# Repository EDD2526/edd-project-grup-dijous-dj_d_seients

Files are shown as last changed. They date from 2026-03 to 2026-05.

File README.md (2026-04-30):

View this project on [CADLAB.io](https://cadlab.io/project/30198). 

# Projecte Grup D (Dijous-tarda): Seients

>**Autors:
- Joan Martínez [@JoaanMG]
- Manel Frías [@manelfriass]
- Joan Heras [@jheraas]

>**Versió: V5.0 (final)

----------

## Objectiu

En primer lloc cal explicar que estem davant de l'elaboració d’un mòdul crític per a la seguretat i el funcionament del vehicle. El sistema de SEIENTS DIGITALS és la interfície entre l'energia del cotxe i la seguretat del conductor.
Per tant ens basarem en aquests puts adjuntats al guió:

  a) 3 motors (posició, alçada, reclinació) amb els seus finals de carrera.
  b) Calefacció del seient. 
  c) Sensor digital de cinturons.
  d) Memòria externa no volàtil per guardar posicions pre-programades.

>PCB per ...

L'objectiu principal és dissenyar i fabricar una PCB funcional per a la gestió del subsistema de seients elèctrics d'un vehicle, complint els següents punts:

- Controlar 3 motors del seient:
- Posició longitudinal, alçada, Inclinació del respatller
- Detectar finals de carrera per evitar sobrecàrregues mecàniques.
- Implementar calefacció del seient amb control electrònic.
- Detectar estat del cinturó de seguretat.
- Guardar i recuperar posicions programades del seient mitjançant memòria no volàtil.
- Permetre la interacció de l’usuari amb botonera.
- Comunicar-se amb la xarxa del vehicle via bus CAN.
- Permetre monitorització i debug via USART.

## Diagrama de blocs

### Descripció/funcionalitat de cada bloc

  - ALIMENTACIÓ: El sistema s’alimenta a partir de la bateria del vehicle (12V). Aquesta tensió es condiciona mitjançant dues etapes. Això permet alimentar:

    * Microcontrolador.
    * Sensors.
    * Comunicacions.
 
  - UART: per debug i monitorització.

  - MICROCONTROLADOR: És el nucli del sistema, encarregat de: Processar les entrades (botons i sensors), controlar els motors, gestionar la comunicació amb altres mòduls. També gestiona diferents interfícies:

    * GPIO → botonera i sensors.
    * PWM → control de motors i calefacció.
    * I2C → memòria i sensor de temperatura.
    * CAN → comunicació amb el vehicle.
    * UART → debug.

  - BOTONERA: Permet a l’usuari controlar el seient:

    * Posició.
    * Alçada.
    * Reclinació.
    
  - SENSORS: de temperatura i cinturons.

  - SISTEMA DE MOTORS.

  - SISTEMA DE CALEFACCIÓ.

  - MEMÒRIA.

  - COMUNICACIÓNS.

-----------

## Requisits / Especificacions

  * Alimentació; 12V, regulada 5V
  * Microcontrolador PIC18xxxxxxxxx
  * ...

-----------

## Components

| Descripci&#243; | Ref | Package |Datasheet | Prove&#239;dor | Value | Preu | Unitats |

| Capacitor | KAF21BR71H104JM | SMD | [Enllaç](https://www.mouser.com/datasheet/3/5926/1/AutoMLCCKAF.pdf) | 100 nF| 0,078 € | x21 |

| Capacitor | KAF21BR71H104JM | SMD | [Enllaç](https://www.mouser.com/datasheet/3/5926/1/AutoMLCCKAF.pdf) | 220 uF| 0,078 € | x2 |

| Capacitor | KAF21BR71H104JM | SMD | [Enllaç](https://www.mouser.com/datasheet/3/5926/1/AutoMLCCKAF.pdf) | 10 uF| 0,078 € | x2 |

| Capacitor | KAF21BR71H104JM | THT | [Enllaç](https://www.mouser.com/datasheet/3/5926/1/AutoMLCCKAF.pdf) | 100 nF| 0,078 € | x2 |

| Capacitor | KAF21BR71H104JM | THT | [Enllaç](https://www.mouser.com/datasheet/3/5926/1/AutoMLCCKAF.pdf) | 100 nF| 0,078 € | x2 |

| Capacitor | KAF21BR71H104JM | SMD | [Enllaç](https://www.mouser.com/datasheet/3/5926/1/AutoMLCCKAF.pdf) | 0.1 uF| 0,078 € | x3 |

| --- | --- | --- | --- | ---| --- | --- |

| Exemple | XYZ1234 | SOT-23 | [Enllaç](https://...) | DigiKey | 2 |

 | Microcontrolador | PIC18F26Q83-I/SS | SOIC-28 |[Datasheet](https://www.mouser.es/datasheet/2/268/PIC18F27_47_57Q83_Preliminary_Data_Sheet_40002265B-2887591.pdf) | [Mouser](https://www.mouser.es/c/?q=PIC18F27Q83-I%2FSO)| 2,17&euro;| 1x |
| XTAL-Ressonador | CSTCR7M99G53-R0 | SMD |[Datasheet](https://www.mouser.es/datasheet/2/281/p16e-522700.pdf) | [Mouser](https://www.mouser.es/ProductDetail/Murata-Electronics/CSTCR7M99G53-R0?qs=Zd9RUO93%2Fo7cnwzsujIkpA%3D%3D)  | 0,27&euro; | 1x |

-----------

## Software

### Eines:

  * KiCad 9.0 o superior
  * 

### Configuraci&#243; :

  * 

### Funcionalitats:

  - Controlar 3 motors del seient:
  - Posició longitudinal, alçada, Inclinació del respatller
  - Detectar finals de carrera per evitar sobrecàrregues mecàniques.
  - Implementar calefacció del seient amb control electrònic.
  - Detectar estat del cinturó de seguretat.
  - Guardar i recuperar posicions programades del seient mitjançant memòria no volàtil.
  - Permetre la interacció de l’usuari amb botonera.
  - Comunicar-se amb la xarxa del vehicle via bus CAN.
  - Permetre monitorització i debug via USART

-----------

## Historial de canvis:

23/03/2026 a les 14:07
Al dia d'avui s'ha modificat el diagrama de blocs: hem ajustat petites coses per finalitzar el diagrama de blocs definitiu.

23/03/2026 a les 17:22
Tan bon punt hem modificat el digrama de blocs, al dia d'avui també s'ha modificat la part sensors: hem incorporat l'esquemàtic preliminar una vegada ajustat el diagrama de blocs. Incorporats el TMP102 (sensor de temperatura) i el Hall A3144 (sensor digital dels cinturons).

24/03/2026 a les 14:07
Al dia d'avui s'ha modificat la part d'alimentació: hem incorporat dues coses importants: FUSIBLE i DIODES TVS. Hem modificat els possibles errors mitjançant una escombrada de l'ERC. Alimentació (ACABAT AL 100%).

24/03/2026 a les 18:48
S'ha modificat la part de SENSORS: una vegada incorporats el TMP102 (sensor de temperatura) i el Hall A3144 (sensor digital dels cinturons) hem realitzat la incorporación dels components: resistències pull-up, capacitats de desacoblament, ...

25/03/2026 a les 09:35
Al dia d'avui s'ha modificat la part de sensors: hem incorporat etiquetes i hem modificat algunes connexions degut a problemes amb l'ERC, SENSORS (ACABAT AL 100%).

25/03/2026 a les 1O:07
S'ha modificat la part de SENSORS: hem finalitzat tot l'esquemàtic d'aquesta part i donem per acabada la part de SENSORS.

25/03/2026 a les 09:35
Efectuada la simulació per demostrar el funcionamenten del LM1117-3.3 (part d'ALIMENTACIÓ) a LTSpice.

| Data | Autor | Branch | Versi&#243; | Descripci&#243; |
| --- | --- | --- | --- | --- |
|  28/03/2023 | mlopez | Master | initial commit | Primera versi&#243; d'esquem&#224;tic i selecci&#243; de components |
E s t a   e s   u n a   l   n e a   d e   p r u e b a   p a r a   e l   r e p o s i t o r i o

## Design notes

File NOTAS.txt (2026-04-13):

SECCIONES:

ALIMENTACIO
POTENCIA (DRIVERS, MOSFET)
SENSORS
DIGITAL/MICROCONTROLADOR/BOTONERA

CALEFACCION METER RELÉ

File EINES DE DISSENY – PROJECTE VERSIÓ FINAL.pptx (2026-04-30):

## EINES DE DISSENY PROJECTE: GRUP D TARDA (SEIENTS)

Joan Martínez
Joan Heras
Manel Frías

## 01 CONTINGUTS 04 03 02

OBJECTIUS DEL PROJECTE

DIAGRAMA DE BLOCS

ESQUEMÀTIC I COMPONENTS

SIMULACIONS

## 05 07 06

LAYOUT I PCB

BOM I PRESSUPOST

RESOURCES

## 01 OBJECTIUS DEL PROJECTE

## OBJECTIUS DEL PROJECTE (Característiques):

En primer lloc cal explicar que estem davant de l'elaboració d’un mòdul crític per a la seguretat i el funcionament del vehicle. El sistema de SEIENTS DIGITALS és la interfície entre l'energia del cotxe i la seguretat del conductor. Per tant ens basarem en aquests puts adjuntats al guió:
a) 3 motors (posició, alçada, reclinació) amb els seus finals de carrera.
b) Calefacció del seient.
c) Sensor digital de cinturons.
d) Memòria externa no volàtil per guardar posicions pre-programades.

## OBJECTIUS PRINCIPALS DEL PROJECTE

L'objectiu principal és dissenyar i fabricar una PCB funcional per a la gestió del subsistema de seients elèctrics d'un vehicle, complint els següents punts:
- Controlar 3 motors del seient:
- Posició longitudinal, alçada, Inclinació del respatller
- Detectar finals de carrera per evitar sobrecàrregues mecàniques.
- Implementar calefacció del seient amb control electrònic.
- Detectar estat del cinturó de seguretat.
- Guardar i recuperar posicions programades del seient mitjançant memòria no volàtil.
- Permetre la interacció de l’usuari amb botonera.
- Comunicar-se amb la xarxa del vehicle via bus CAN.
- Permetre monitorització i debug via USART.c

## 02 DIAGRAMA DE BLOCS

## V.2

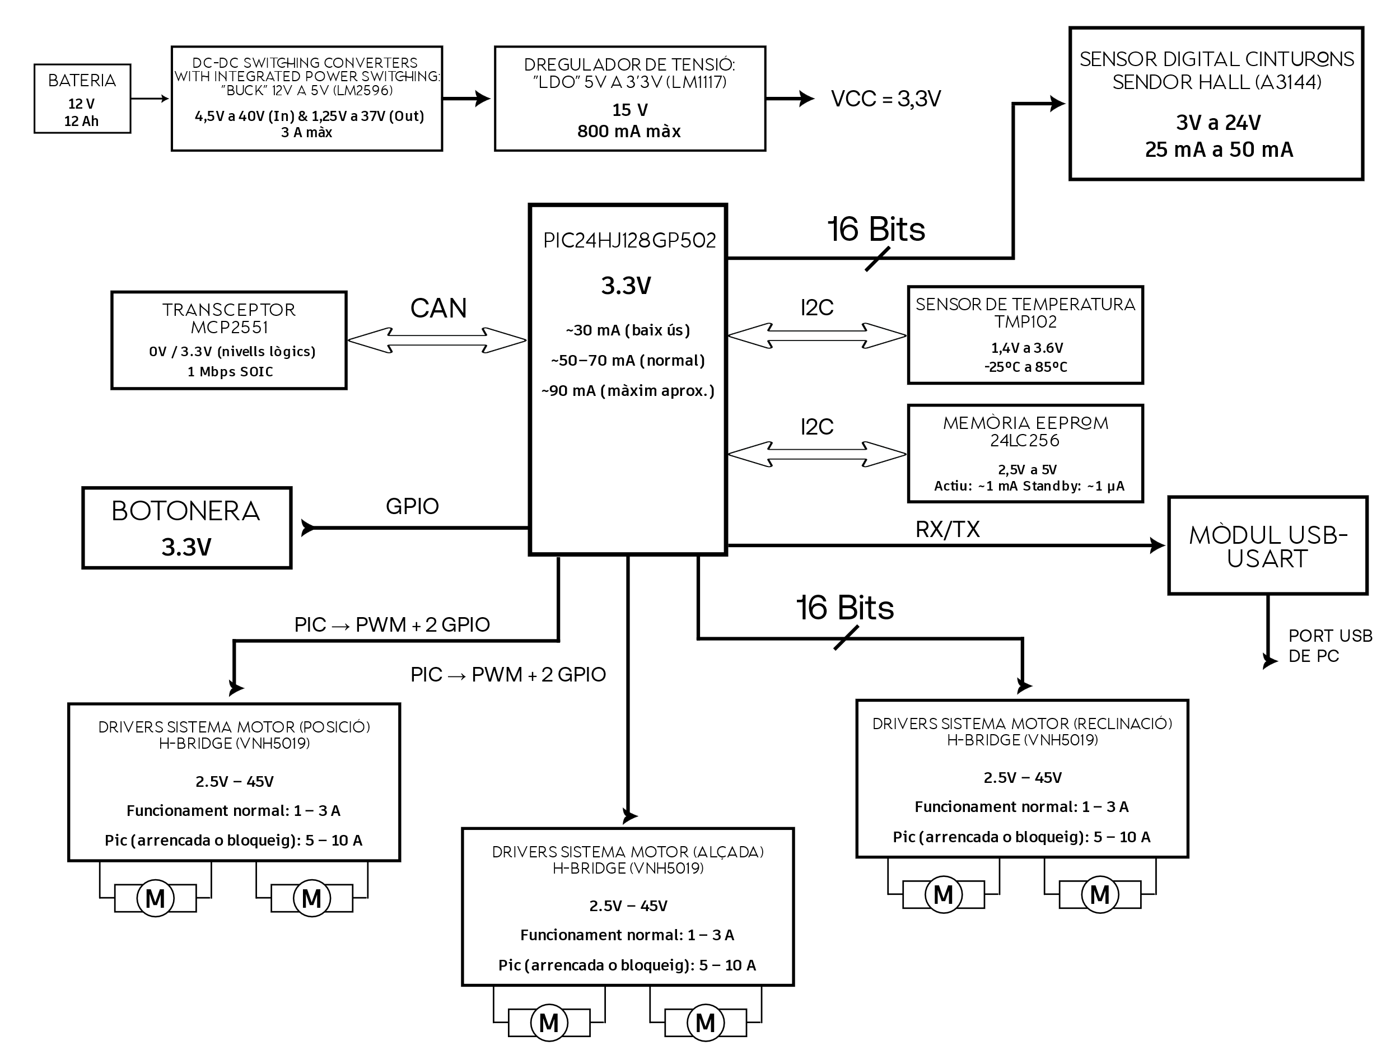
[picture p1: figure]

## V.3

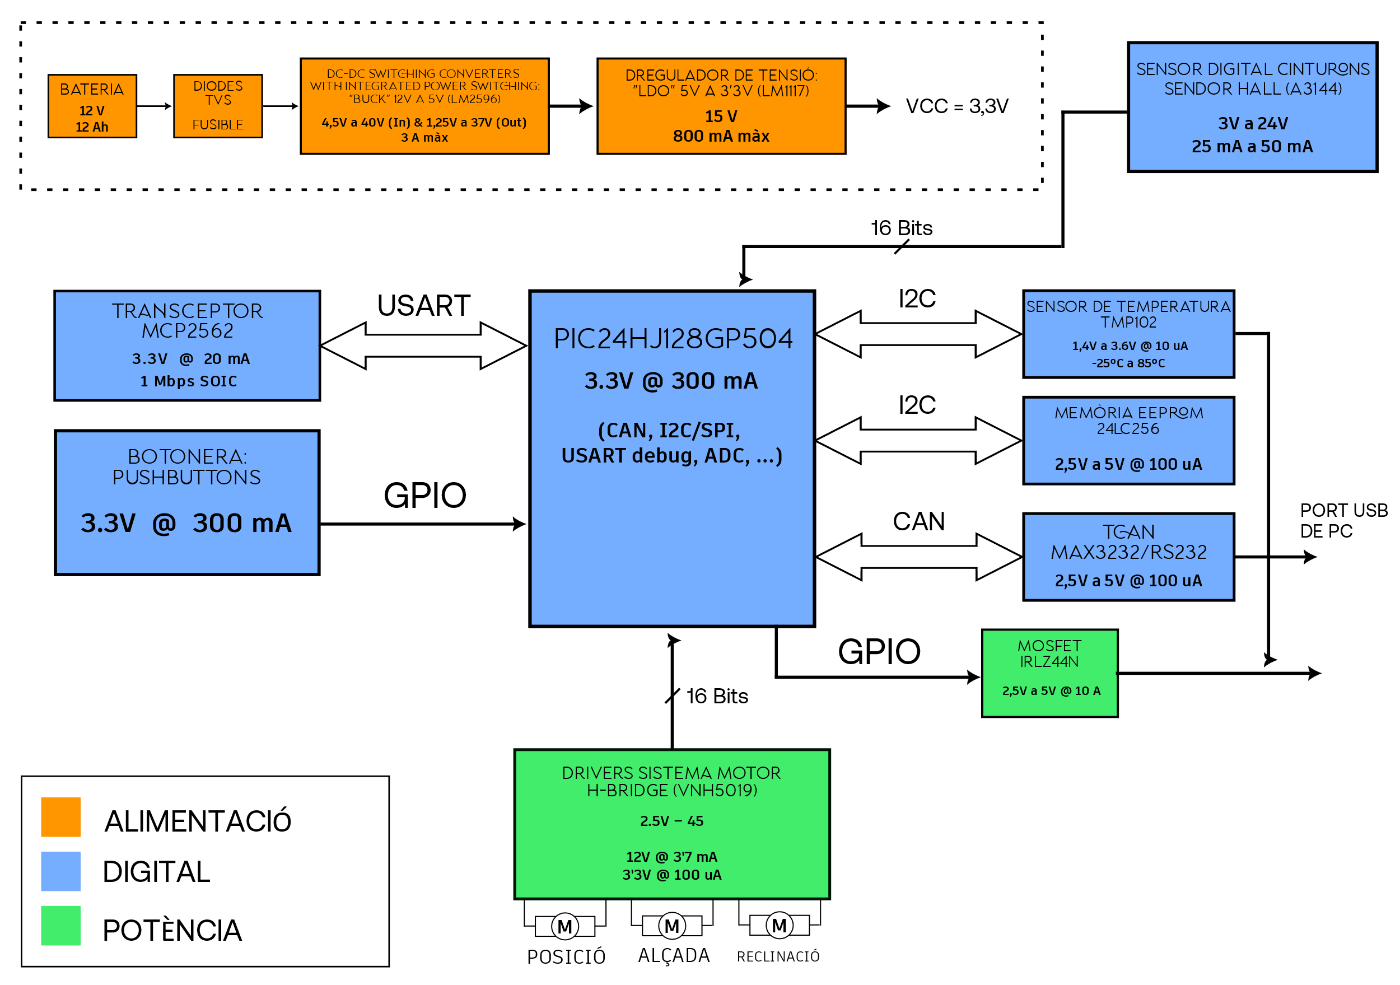
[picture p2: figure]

## ESQUEMÀTIC DEL PROJECTE 03

## ALIMENTACIÓ:

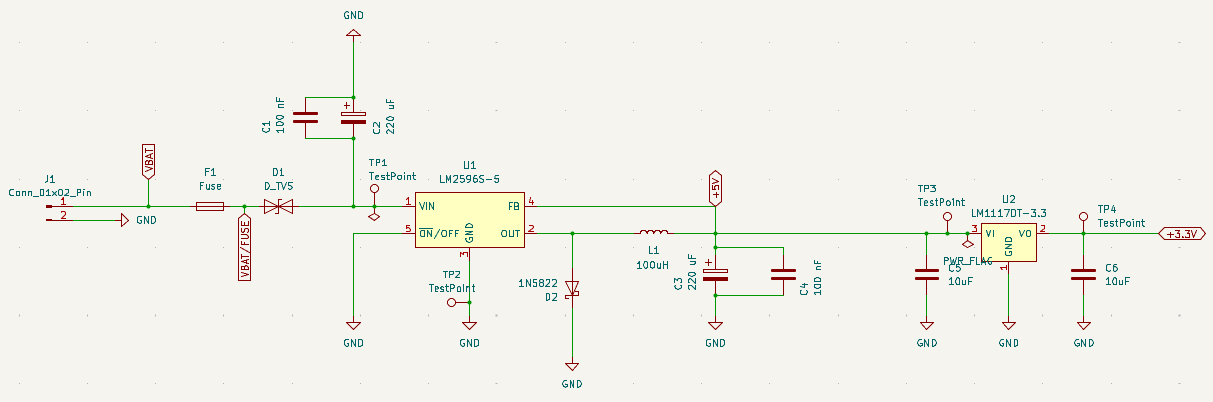
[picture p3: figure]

## SENSORS:

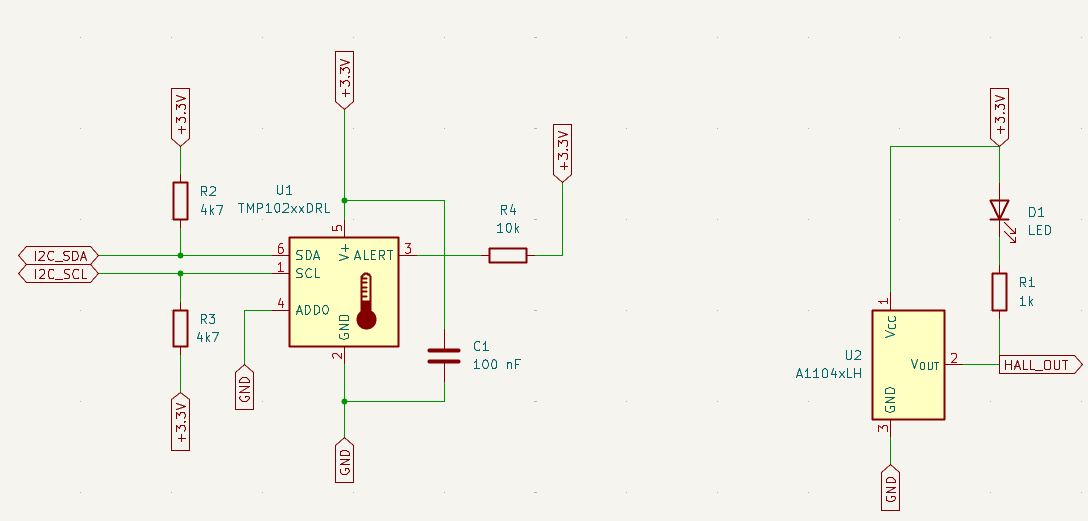
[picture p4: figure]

V.2

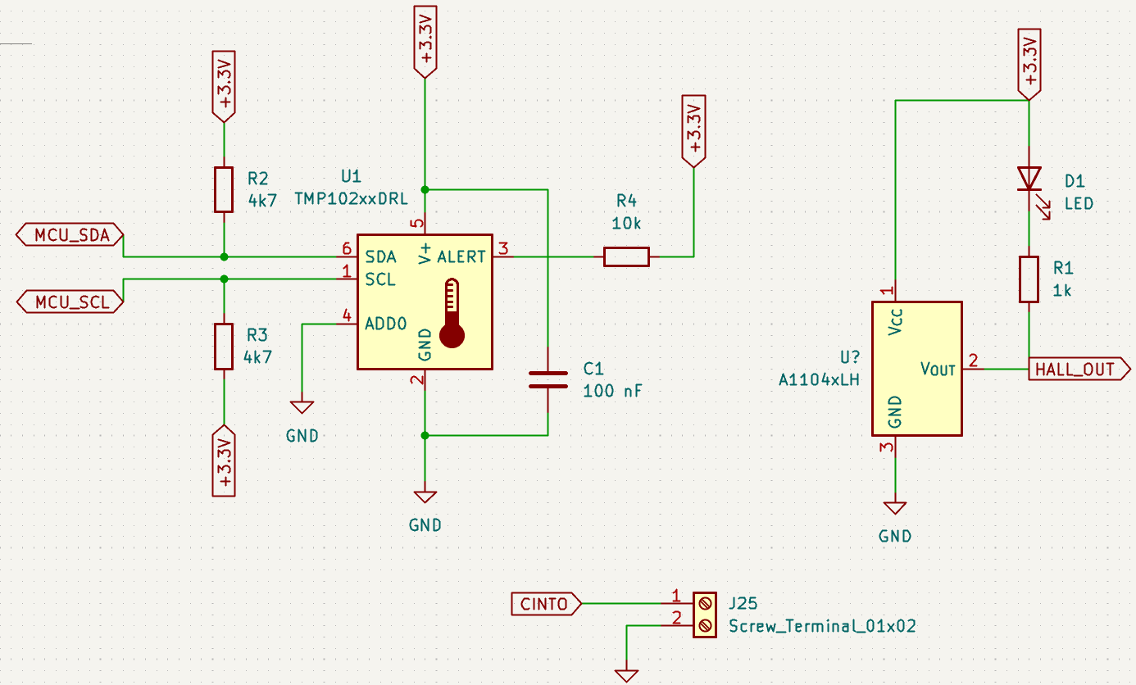
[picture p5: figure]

V.3

## DRIVERS:

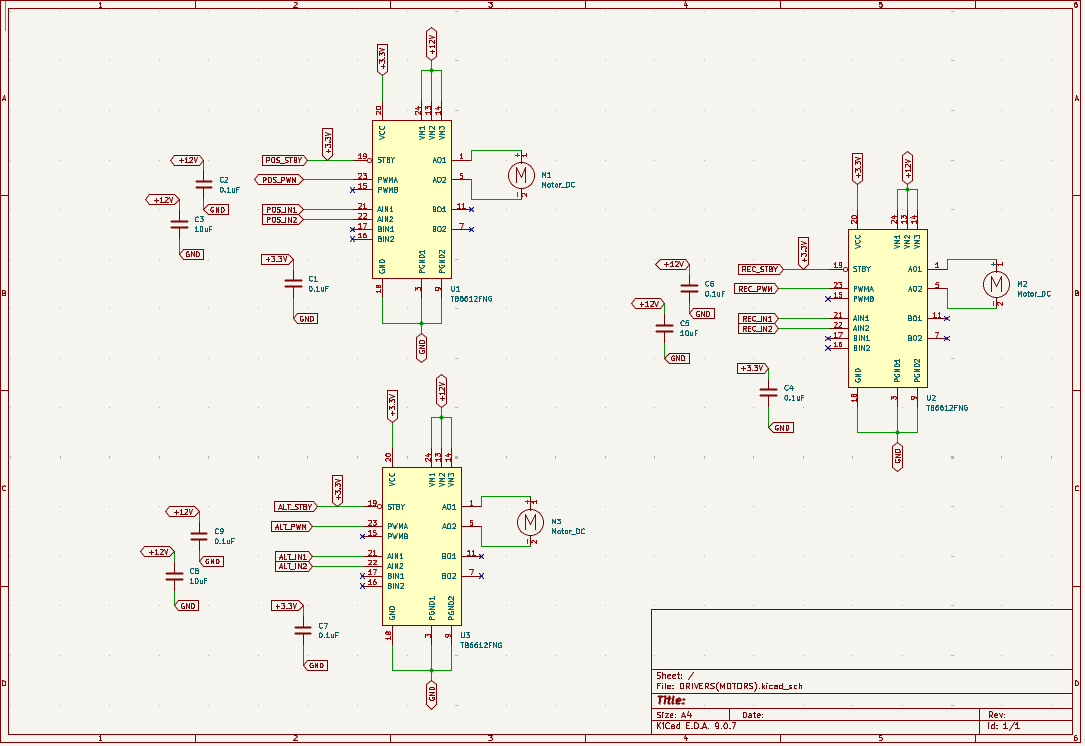
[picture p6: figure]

V.2

## DRIVERS:

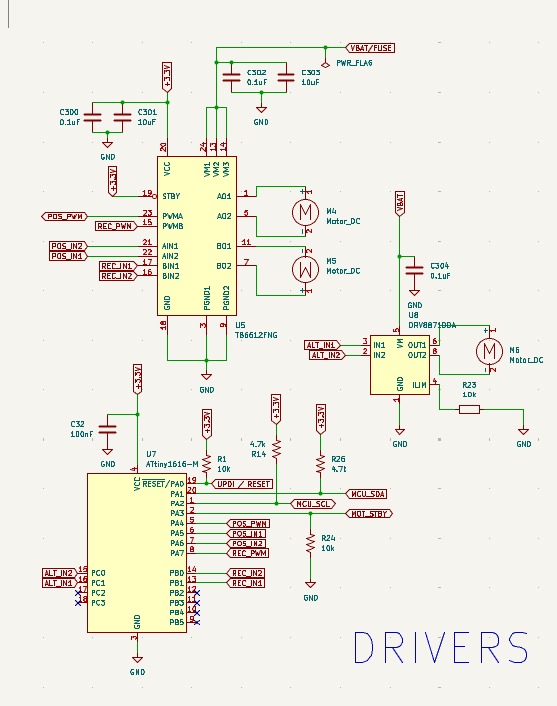
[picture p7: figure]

V.3

## EEPROM:

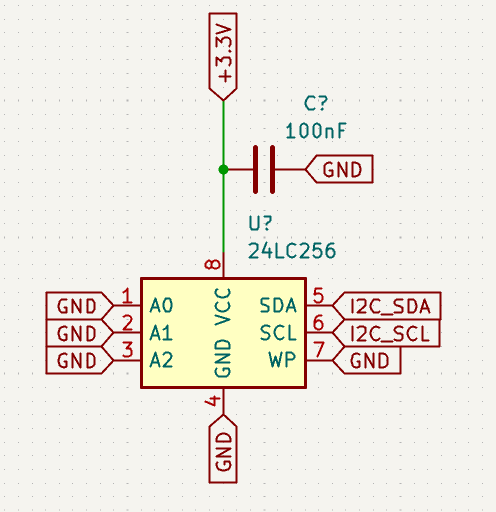
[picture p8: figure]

V.2

## EEPROM:

V.3

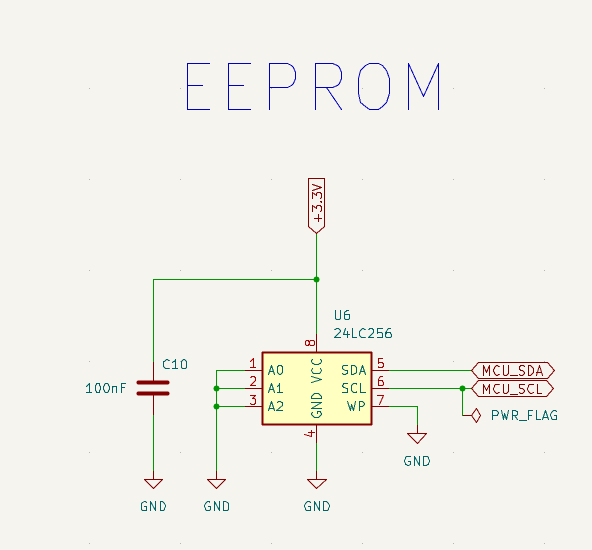
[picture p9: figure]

## MOSFET:

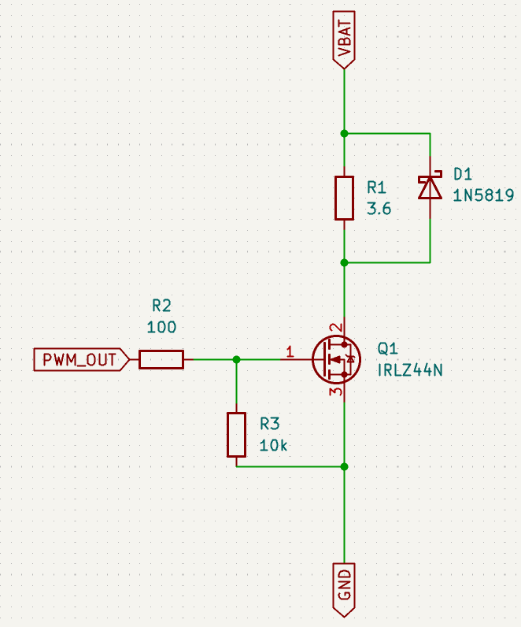
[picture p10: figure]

V.2

## MOSFET:

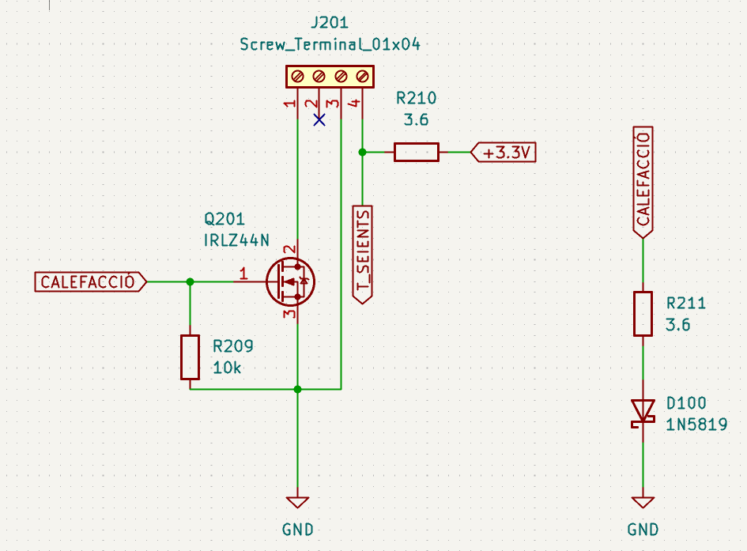
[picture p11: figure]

V.3

## CAN/DE-9:

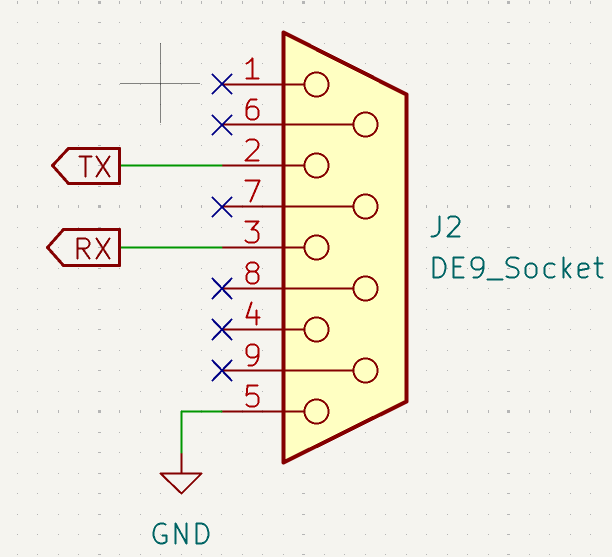
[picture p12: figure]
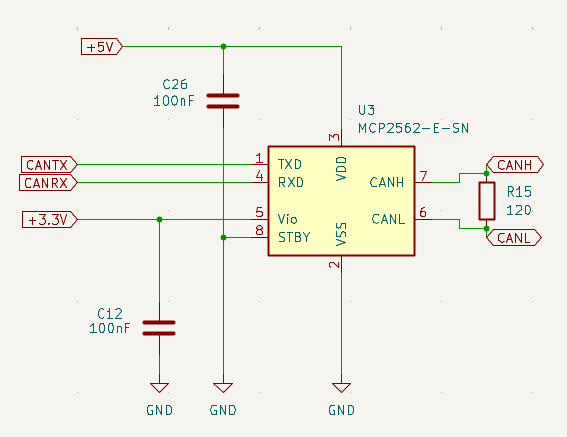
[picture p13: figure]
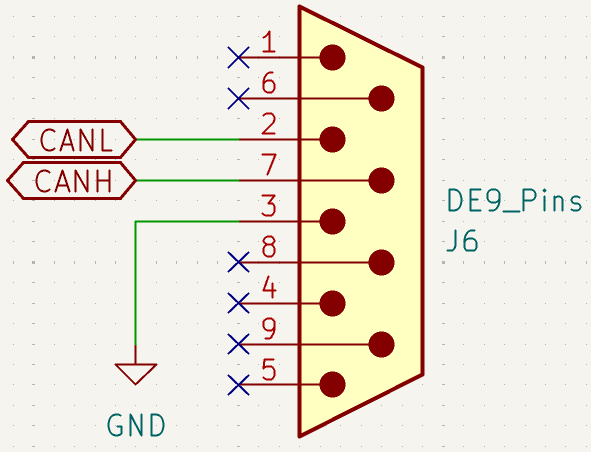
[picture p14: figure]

## BOTONERA:

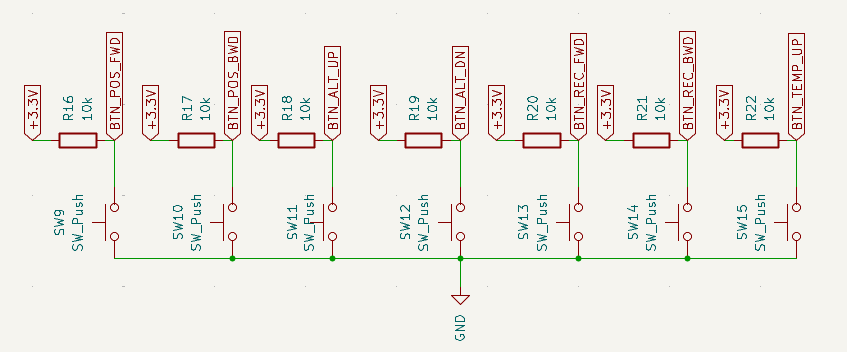
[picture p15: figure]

## MICROCONTROLADOR:

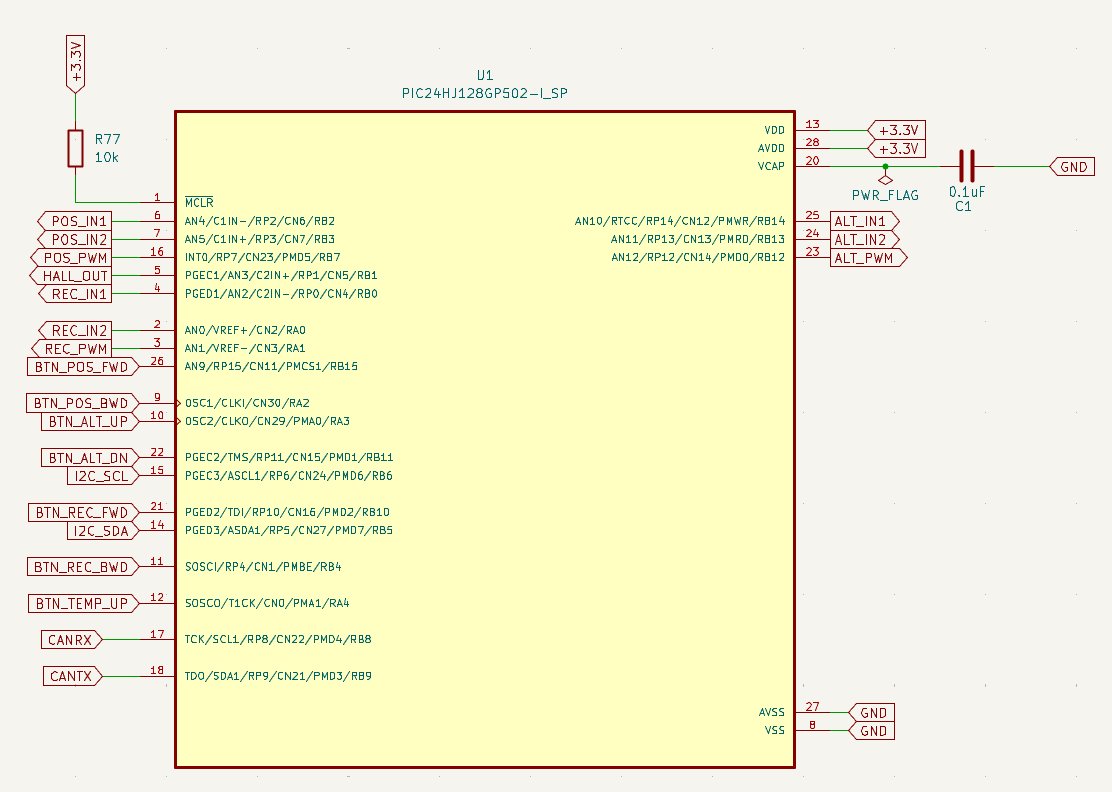
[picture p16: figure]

V.2

## MICROCONTROLADOR:

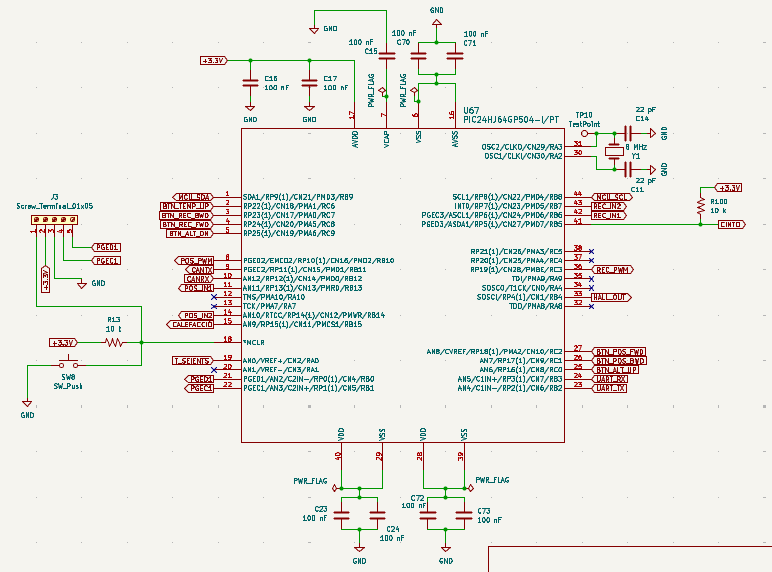
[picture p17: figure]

V.3

## SIMULACIONS LTSPICE 04

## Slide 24

En particular, s’ha simulat el regulador de tensió (LM1117) amb diferents condicions de càrrega per comprovar la seva capacitat de mantenir una tensió estable de 3.3V davant variacions de corrent:

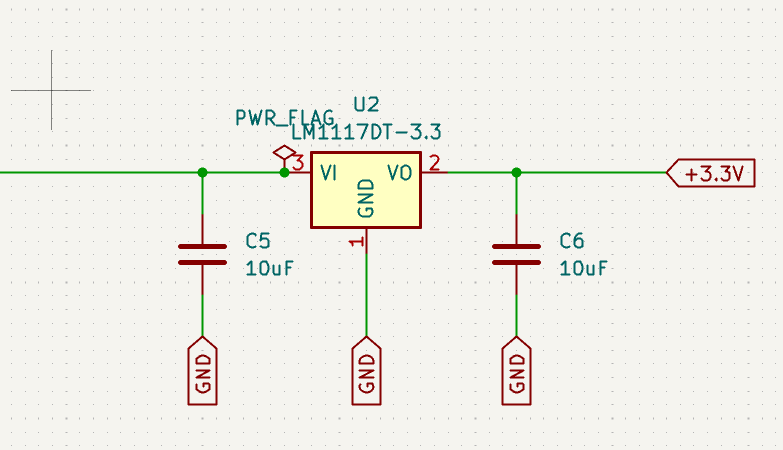
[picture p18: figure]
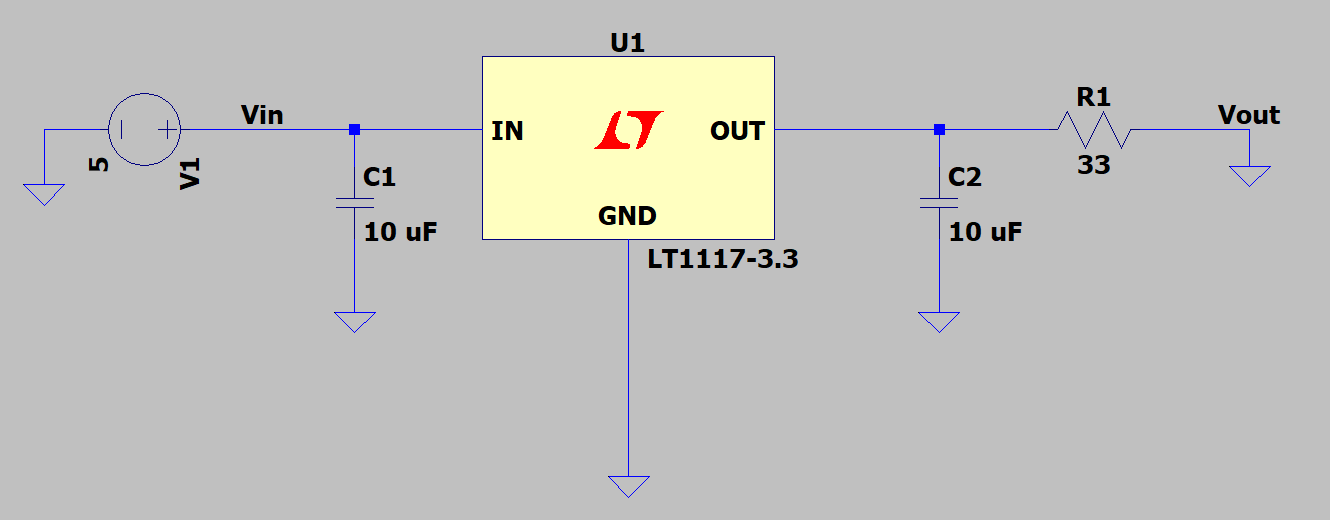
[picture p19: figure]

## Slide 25

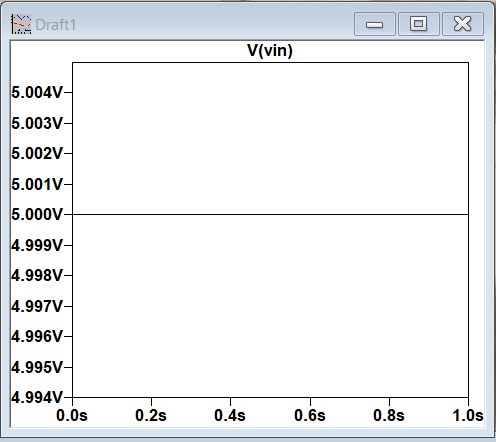
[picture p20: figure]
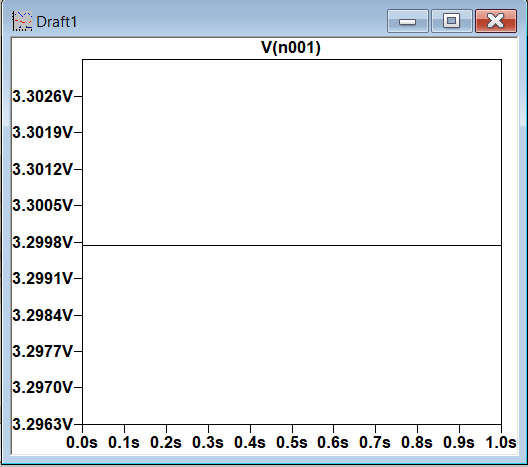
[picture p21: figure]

## LAYOUT I PCB 05

## BOM I COSTOS 06

## PRESSUPOST DE FABRICACIÓ

Vam procedir a crear un compte a Mouser Electronics, Inc. Vam crear un projecte nou el qual es va exportar el BOM creat pel KICad i tots els components que hem utilitzat van quedar enregistrats en un altre arxiu de fulla de càlcul (.xlxs).

## PRESSUPOST DE FABRICACIÓ:

Com a idea general, el cost del projecte no és fix, sinó que depèn principalment de:

VOLUM DE PRODUCCIÓ

## PRESSUPOST DE FABRICACIÓ:

l el projecte demana analitzar:
    - x10 unitats
    - x50 unitats
    - x1.000 unitats
    - x20.000 unitats

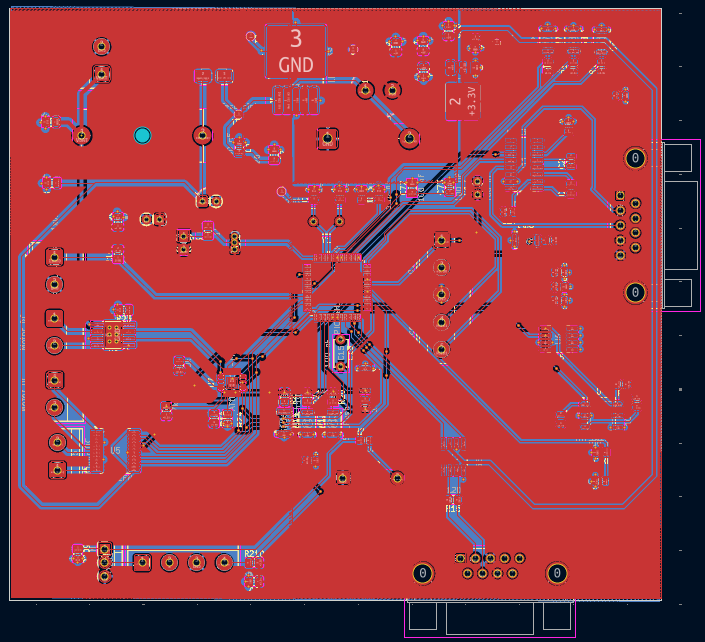
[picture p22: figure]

## PRESSUPOST DE FABRICACIÓ:

Volum (per unitats) | Cost total
x1 unitats | 63,863 €
x10 unitats | 638,63 €
x50 unitats | 3193.15 €
x1.000 unitats | 63.863 €
x20.000 unitats | 1.277.260 €

## PRESSUPOST DE FABRICACIÓ:

1. Components (BOM)
2. Fabricació de la PCB
3. Muntatge

Segons el document, el cost es divideix en:

## PRESSUPOST DE FABRICACIÓ:

l què passa amb el cost?
- A mesura que augmenta la producció:
- L’anàlisi de costos mostra que el preu del sistema depèn fortament del volum de producció, reduint-se significativament en producció massiva gràcies a economies d’escala i processos de fabricació automatitzats.

EL COST PER UNITAT BAIXA

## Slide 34

COMPONENTS | PREU (€)
MAX3232 | 9.15
Regulador switching | 5.99
Microcontrolador | 5.74
Inductor | 4.68
Connector D-Sub | 2.91
Terminal blocks | 2.39
Driver motor | 2.35
MOSFET | 1.52

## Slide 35

El cost total creix linealment amb el volum, però el cost per unitat disminuiria en producció real gràcies a economies d’escala.

## QUINA CONCLUSIÓ PODEM EXTREURE ?

En primer lloc podem afirmar que els components passius dominen la taula. El cost per PCB és d’aproximadament 54€, dominat pels components actius del sistema. Els components més cars són el microcontrolador, els drivers i els reguladors, mentre que els passius tenen un impacte econòmic molt reduït
Finalment, si s’efectua una producció massiva, el cost per unitat es reduiria significativament gràcies a descomptes i optimització del procés de fabricació.

## RESOURCES 07

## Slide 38

Webgrafia:
- Microchip Technology. (2012). PIC24HJ128GP502 Family Data Sheet. High-Performance, 16-bit Digital Signal Controllers. [En línia]. Disponible a: microchip.com
- Microchip Technology. (2016). MCP2561/2 High-Speed CAN Transceiver Data Sheet. [En línia].Texas Instruments. (2020). LM1117 800-mA, Low-Dropout Voltage Regulator. [En línia]. Disponible a: ti.com
- Infineon Technologies. (2023). Automotive MOSFETs Selection Guide.
- Vector Informatik GmbH. (2024). CAN Knowledge Base. [web]. vector.com.
- All About Circuits. (2024). Understanding the I2C Bus. [Article tècnic]. Disponible a: allaboutcircuits.com.
- Microchip Developer Help. Getting Started with MPLAB X IDE and XC16 Compiler. [Portal de suport].

## GRÀCIES!

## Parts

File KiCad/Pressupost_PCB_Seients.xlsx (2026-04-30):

Cost total del projecte: Components + PCB + muntatge | Cost total del projecte: Components + PCB + muntatge | Cost total del projecte: Components + PCB + muntatge | Cost total del projecte: Components + PCB + muntatge | Cost total del projecte: Components + PCB + muntatge | Cost total del projecte: Components + PCB + muntatge | Cost total del projecte: Components + PCB + muntatge | Cost total del projecte: Components + PCB + muntatge | Cost total del projecte: Components + PCB + muntatge
Paràmetre | Valor | Notes |  |  |  |  |  |  | Component crític | Cost aproximat | Motiu
Cost BOM per PCB | €65.9150 | Calculat del BOM Mouser: sum(Unit Price × Order Quantity) |  |  |  |  |  |  | RS-232 / UART interface | €9.15 | Component més car del BOM
Juntes SMT per PCB | €220.0000 | Estimació per al càlcul de muntatge |  |  |  |  |  |  | Regulador switching | €5.99 | Etapa d'alimentació
Juntes manuals per PCB | €30.0000 | Connectors/through-hole o muntatge manual |  |  |  |  |  |  | Microcontrolador PIC24 | €5.74 | Control principal
Setup muntatge | €25.0000 | Cost fix |  |  |  |  |  |  | Inductor | €4.68 | Etapa buck
Stencil | €7.8600 | Cost fix |  |  |  |  |  |  | Connector D-Sub | €2.91 | Comunicacions externes
Panel fee | €7.8100 | Cost fix
Cost SMT per junta | €0.0016 | Cost variable
Cost manual per junta | €0.0157 | Cost variable
PCB bare board total | Estimació | Substituir pel pressupost real de JLCPCB quan tingueu Gerbers
Volum | BOM €/PCB | BOM total € | PCB €/PCB | PCB total € | Muntatge €/PCB | Muntatge total € | Cost total €/PCB | Cost total €
10 | €65.92 | €659.15 | €2.50 | €25.00 | €4.89 | €48.90 | €73.31 | €733.05
50 | €65.92 | €3295.75 | €1.40 | €70.00 | €1.64 | €81.82 | €68.95 | €3447.57
1000 | €65.92 | €65915.00 | €0.50 | €500.00 | €0.86 | €863.67 | €67.28 | €67278.67
20000 | €65.92 | €1318300.00 | €0.30 | €6000.00 | €0.83 | €16500.67 | €67.04 | €1340800.67

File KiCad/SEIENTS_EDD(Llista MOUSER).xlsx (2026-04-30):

Mouser Part Number (Input) | Mfr Part Number | Mouser Part Number | Manufacturer Name | Description | Unit Price 1 (EUR) | Price 2 (EUR) | Price 3 (EUR) | Order Quantity | Order Unit Price (EUR) | Price by Order Unit (EUR) | Price 5 (EUR) | Min./Mult. | Availability | Lead Time in Days | Lead Time in Weeks | Lifecycle | NCNR | RoHS | Pb Free | Package Type | Package Quantity | Datasheet URL | Product Image | Design Risk
KAF21BR71H104JM | KAF21BR71H104JM | 581-KAF21BR71H104JM | KYOCERA AVX | Multilayer Ceramic Capacitors MLCC - SMD/SMT Multilayer Ceramic Capacitors MLCC - SMD/SMT Automotive 0805, 100nF, 5%, X7R, 50V | 0,078 € |  |  | 21 | 0,078 € | 1.638 |  | 1/1 | 40.051 | 84 | 12 |  | No | Yes | Yes | REEL | 15.000 | https://www.mouser.com/datasheet/3/5926/1/AutoMLCCKAF.pdf |  | Product has high popularity and is readily available.
08053F224K4T2A | 08053F224K4T2A | 581-08053F224K4T2A | KYOCERA AVX | Multilayer Ceramic Capacitors MLCC - SMD/SMT Multilayer Ceramic Capacitors MLCC - SMD/SMT PN CHANGE NEW PN KAM21AR81E224KU SEE ATTACHED DOCUMENT | 0,378 € |  |  | 2 | 0,378 € | 0.756 |  | 1/1 | 3.218 | 84 | 12 | New at Mouser | No | Yes | Yes | REEL | 2.000 | https://www.mouser.com/datasheet/3/5926/1/HighTempX8RX8L.pdf |  | Product is new and is readily available.
C0805X106K9RACAUTO | C0805X106K9RACAUTO | 80-C0805X106K9RAUTO | KEMET | Multilayer Ceramic Capacitors MLCC - SMD/SMT Multilayer Ceramic Capacitors MLCC - SMD/SMT 6.3 V 10 uF 0805 X7R 10 % AECQ200 | 0,774 € |  |  | 2 | 0,774 € | 1.548 |  | 1/1 | 10.455 | 245 | 35 |  | No | Yes | Yes | REEL | 2.500 | https://www.mouser.com/datasheet/3/72/1/C0805X106K9RACAUTO.pdf |  | Product has high popularity and is readily available.
08052C223M4Z2A | 08052C223M4Z2A | 581-08052C223M4Z2A | KYOCERA AVX | Multilayer Ceramic Capacitors MLCC - SMD/SMT Multilayer Ceramic Capacitors MLCC - SMD/SMT PN CHANGE NEW PN KAF21KR72D223MU SEE ATTACHED DOCUMENT | 0,224 € |  |  | 2 | 0,224 € | 0.448 |  | 1/1 | 9.283 | 84 | 12 | New Product | No | Yes | Yes | REEL | 2.000 | https://datasheets.kyocera-avx.com/AutoMLCC.pdf |  | Product is new and is readily available.
SMAJ12A | SMAJ12A | 821-SMAJ12AM2G | Taiwan Semiconductor | ESD Protection Diodes / TVS Diodes ESD Protection Diodes / TVS Diodes 400W, 14V, 5%, Unidirectional, TVS | 0,344 € |  |  | 1 | 0,344 € | 0.344 |  | 1/1 | 9.768 | 133 | 19 |  | No | Yes | No | REEL | 7.500 | https://www.taiwansemi.com/assets/datasheet/pdf.php?pn=SMAJ12A |  | Product has high popularity and is readily available.
1N5822 | 1N5822 | 821-1N5822 | Taiwan Semiconductor | Schottky Diodes & Rectifiers Schottky Diodes & Rectifiers 3A, 40V, Schottky Rectifier | 0,525 € |  |  | 1 | 0,525 € | 0.525 |  | 1/1 | 3.149 | 56 | 8 |  | No | Yes | No | REEL | 1.250 | https://www.taiwansemi.com/assets/datasheet/pdf.php?pn=1N5822 |  | Product has high popularity and is readily available.
C566E-AFE-CV34Q342 | C566E-AFE-CV34Q342 | 941-C566EAFECV34Q342 | Cree LED | Single Color LEDs Single Color LEDs | 0,163 € |  |  | 1 | 0,163 € | 0.163 |  | 1/1 | 30.931 | 28 | 4 | New Product | No | Yes | Yes | AMMO PACK | 3.000 | https://downloads.cree-led.com/files/ds/h/HB-C556E.pdf |  | Product is new and is readily available.
1N5819 | 1N5819 | 821-1N5819 | Taiwan Semiconductor | Schottky Diodes & Rectifiers Schottky Diodes & Rectifiers 1A, 40V, Schottky Rectifier | 0,258 € |  |  | 1 | 0,258 € | 0.258 |  | 1/1 | 10.220 | 56 | 8 |  | No | Yes | No | REEL | 5.000 | https://www.taiwansemi.com/assets/datasheet/pdf.php?pn=1N5819 |  | Product has high popularity and is readily available.
LFXTAL029665Reel | LFXTAL029665Reel | 449-LFXTAL029665REEL | IQD Frequency Products | Crystals Crystals 8MHz 16pF -10C 60C | 0,568 € |  |  | 1 | 0,568 € | 0.568 |  | 1/1 | 2.830 | 69 | 10 |  | No | Yes | Yes | REEL | 1.000 | https://www.mouser.com/datasheet/3/1460/1/LFXTAL029665B.pdf |  | Product has high popularity and is readily available.
PIC24HJ64GP504-I/PT | PIC24HJ64GP504-I/PT | 579-PIC24H64GP504IPT | Microchip | 16-bit Microcontrollers - MCU 16-bit Microcontrollers - MCU 16B MCU 64KB DMA 40MIPS | 5,74 € |  |  | 1 | 5,74 € | 5.74 |  | 1/1 | 4.055 | 49 | 7 |  | No | Yes | No | TRAY | 160 | https://www.mouser.com/datasheet/3/282/1/70293G.pdf |  | Product has high popularity and is readily available.
MAX3232 | MAX3232CPE+ | 700-MAX3232CPE | Analog Devices Inc. | RS-232 Interface IC RS-232 Interface IC 3.0V to 5.5V, Low-Power, up to 1Mbps, Tr | 9,15 € |  |  | 1 | 9,15 € | 9.15 |  | 1/1 | 836 | 70 | 10 |  | No | Yes | Yes | TUBE | 25 | https://www.mouser.com/datasheet/3/1014/1/MAX3222-MAX3241.pdf |  | Product has high popularity and is readily available.
DRV8871DDAR | DRV8871DDAR | 595-DRV8871DDAR | Texas Instruments | Motor / Motion / Ignition Controllers & Drivers Motor / Motion / Ignition Controllers & Drivers 50-V 3.6-A H-bridge motor driver with i A 595-DRV8871DDA | 2,35 € |  |  | 1 | 2,35 € | 2.35 |  | 1/1 | 5.955 | 84 | 12 |  | No | Yes | No | REEL | 2.500 | https://www.ti.com/lit/gpn/drv8871-q1 |  | Product has high popularity and is readily available.
ATTINY1616-M | ATTINY1616-MZ-VAO | 579-ATTINY1616MZVAO | Microchip | 8-bit Microcontrollers - MCU 8-bit Microcontrollers - MCU 16MHz, 16KB, QFN20 Wettable flanks, Auto 125C, Green, Tray | 0,86 € |  |  | 1 | 0,86 € | 0.86 |  | 1/1 | 670 | 28 | 4 | New Product | No | Yes | No | TRAY | 490 | https://ww1.microchip.com/downloads/aemDocuments/documents/OTH/ProductDocuments/DataSheets/ATtiny1614-1616-1617-Auto-DataSheet-DS40002021C.pdf |  | Product is new and is readily available.
24LC256 | 24LC256-E/MS | 579-24LC256-E/MS | Microchip | EEPROM EEPROM 32kx8 - 2.5V | 1,04 € |  |  | 1 | 1,04 € | 1.04 |  | 1/1 | 662 | 56 | 8 |  | No | Yes | Yes | TUBE | 100 | https://www.mouser.com/datasheet/3/282/1/24AA256_24LC256_24FC256_256K_I2C_Serial_EEPROM_DS20001203.pdf |  | Product has high popularity and is readily available.
TB6612FNG,C,8,EL | TB6612FNG,C,8,EL | 757-TB6612FNGC8EL | Toshiba | Motor / Motion / Ignition Controllers & Drivers Motor / Motion / Ignition Controllers & Drivers Brush Motor Driver IC | 1,57 € |  |  | 1 | 1,57 € | 1.57 |  | 1/1 | 9.236 | 161 | 23 |  | No | Yes | Yes | REEL | 2.000 | https://www.mouser.com/datasheet/3/1466/1/216DCAEB880587735ABECF157C737FDE2A898DFC34EBA4541BB25F243D84D2B0.pdf |  | Product has high popularity and is readily available.
TMP102AQDRLRQ1 | TMP102AQDRLRQ1 | 595-TMP102AQDRLRQ1 | Texas Instruments | Board Mount Temperature Sensors Board Mount Temperature Sensors Automotive Grade Dig Temperatu Sensor | 1,01 € |  |  | 1 | 1,01 € | 1.01 |  | 1/1 |  | 84 | 12 |  | No | Yes | No | REEL | 4.000 | https://www.ti.com/lit/gpn/tmp102-q1 |  | Product has high popularity and is readily available.
MCP2562-E/SN | MCP2562-E/SN | 579-MCP2562-E/SN | Microchip | CAN Interface IC CAN Interface IC CAN Tranceiver | 1,04 € |  |  | 1 | 1,04 € | 1.04 |  | 1/1 | 4.295 | 24 | 4 |  | No | Yes | No | TUBE | 100 | https://www.mouser.com/datasheet/3/282/1/20005167C.pdf |  | Product has high popularity and is readily available.
LM1117DT-3.3/NOPB | LM1117DT-3.3/NOPB | 926-LM1117DT-3.3NOPB | Texas Instruments | LDO Voltage Regulators LDO Voltage Regulators 800MA LDO LINEAR REG A 926-LM1117DTX3.3N A 926-LM1117DTX3.3NOPB | 1,47 € |  |  | 1 | 1,47 € | 1.47 |  | 1/1 | 7.534 | 126 | 18 |  | No | Yes | Yes | TUBE | 75 | https://www.ti.com/lit/gpn/lm1117 |  | Product has high popularity and is readily available.
LM2596S-5.0/NOPB | LM2596S-5.0/NOPB | 926-LM2596S-5.0/NOPB | Texas Instruments | Switching Voltage Regulators Switching Voltage Regulators 150 KHZ 3A STEP-DOWN VLTG REG A 926-LM25 A 926-LM2596SX-5.0NOPB | 5,99 € |  |  | 1 | 5,99 € | 5.99 |  | 1/1 | 2.717 | 84 | 12 |  | No | Yes | No | TUBE | 45 | https://www.ti.com/lit/gpn/lm2596 |  | Product has high popularity and is readily available.
SKRKAGE020 | SKRKAGE020 | 688-SKRKAG | Alps Alpine | Tactile Switches Tactile Switches 3.9X2.9X1.5mm 160gf | 0,454 € |  |  | 8 | 0,454 € | 3.632 |  | 1/1 | 239 | 224 | 32 |  | No | Yes | No | REEL | 5.000 | https://www.alps.com/prod/info/E/PDF/Tact/SurfaceMount/SKRK/SKRK.pdf |  | Product has high popularity and is readily available.
ERJ-6RQJ3R6V | ERJ-6RQJ3R6V | 667-ERJ-6RQJ3R6V | Panasonic | Current Sense Resistors - SMD Current Sense Resistors - SMD 0805 3.6ohm 5% Curr Sense AEC-Q200 | 0,37 € |  |  | 2 | 0,37 € | 0.74 |  | 1/1 | 4.316 | 84 | 12 |  | No | Yes | No | REEL | 5.000 | https://industrial.panasonic.com/cdbs/www-data/pdf/RDO0000/RDO0000C334.pdf |  | Product has moderate popularity and is readily available.
CHP0805-FX-1200ELF | CHP0805-FX-1200ELF | 652-CHP0805FX1200ELF | Bourns | Thick Film Resistors - SMD Thick Film Resistors - SMD ResHighPower 0805 120R 1% 1/2W TC100 | 0,344 € |  |  | 1 | 0,344 € | 0.344 |  | 1/1 | 8.898 | 98 | 14 |  | No | Yes | No | REEL | 5.000 | https://www.mouser.com/datasheet/3/40/1/chp.pdf |  | Product has high popularity and is readily available.
RC0805FR-074K7L | RC0805FR-074K7L | 603-RC0805FR-074K7L | YAGEO | Thick Film Resistors - SMD Thick Film Resistors - SMD General Purpose Chip Resistor 0805, 4.7kOhms, 1%, 1/8W | 0,086 € |  |  | 4 | 0,086 € | 0.344 |  | 1/1 | 738.983 | 126 | 18 |  | No | Yes | No | REEL | 5.000 | https://www.mouser.com/catalog/specsheets/YAGEO_PYu_RC_Group_51_RoHS_L_12.pdf |  | Product has high popularity and is readily available.
ERJ-S06F1002V | ERJ-S06F1002V | 667-ERJ-S06F1002V | Panasonic | Thick Film Resistors - SMD Thick Film Resistors - SMD 0805 10Kohms 1% Anti-Sulfur | 0,267 € |  |  | 12 | 0,096 € | 1.152 |  | 1/1 | 4.453 | 84 | 12 |  | No | Yes | No | REEL | 5.000 | https://industrial.panasonic.com/cdbs/www-data/pdf/RDO0000/RDO0000C334.pdf |  | Product has high popularity and is readily available.
SDR10EZPF1001 | SDR10EZPF1001 | 755-SDR10EZPF1001 | ROHM Semiconductor | Thick Film Resistors - SMD Thick Film Resistors - SMD Anti-Surge Chip Resistor, 2012mm 400V 0.66W +/-1%, 1,000 Ohm | 0,189 € |  |  | 1 | 0,189 € | 0.189 |  | 1/1 | 9.261 | 63 | 9 |  | No | Yes | Yes | REEL | 5.000 | https://www.rohm.com/datasheet?p=SDR10EZPF&dist=Mouser&media=referral&campaign=Mouser |  | Product has moderate popularity and is readily available.
IRLZ44NPBF | IRLZ44NPBF | 942-IRLZ44NPBF | Infineon | MOSFETs MOSFETs MOSFT 55V 47A 22mOhm 32nC LogLvlAB | 1,52 € |  |  | 1 | 1,52 € | 1.52 |  | 1/1 | 47.229 | 182 | 26 |  | No | Yes | Yes | TUBE | 1.000 | https://www.mouser.com/datasheet/3/70/1/Infineon_IRLZ44N_DataSheet_v01_01_EN.pdf |  | Product has high popularity and is readily available.
70F101AF-RC | 70F101AF-RC | 542-70F101-RC | Bourns | RF Inductors - Leaded RF Inductors - Leaded 100mH 5% | 4,68 € |  |  | 1 | 4,68 € | 4.68 |  | 1/1 | 463 | 98 | 14 |  | No | Yes | Yes | BULK | 600 | https://www.mouser.com/datasheet/3/40/1/70f_series.pdf |  | Product has moderate popularity and is readily available.
A1104EUA-T | A1104EUA-T | 250-A1104EUA-T | Allegro MicroSystems | Board Mount Hall Effect / Magnetic Sensors Board Mount Hall Effect / Magnetic Sensors CONTINUOUS TIME HALL-EFFECT SWITCH | 1,04 € |  |  | 1 | 1,04 € | 1.04 |  | 1/1 | 6.002 | 168 | 24 |  | No | Yes | Yes | BULK | 4.000 | https://www.allegromicro.com/~/media/files/datasheets/a110x-datasheet.pdf |  | Product has high popularity and is readily available.
FG24X7R2A104KNT00 | FG24X7R2A104KNT00 | 810-FG24X7R2A104KNT0 | TDK | Multilayer Ceramic Capacitors MLCC - Leaded Multilayer Ceramic Capacitors MLCC - Leaded RAD 100V 0.1uF X7R 10% LS:5mm | 0,327 € |  |  | 2 | 0,327 € | 0.654 |  | 1/1 | 800 | 168 | 24 |  | No | Yes | Yes | BULK | 500 | https://product.tdk.com/system/files/dam/doc/product/capacitor/ceramic/lead-mlcc/catalog/leadmlcc_halogenfree_fg_en.pdf |  | Product has high popularity and is readily available.
K104K15X7RF53L2 | K104K15X7RF53L2 | 594-K104K15X7RF53L2 | Vishay | Multilayer Ceramic Capacitors MLCC - Leaded Multilayer Ceramic Capacitors MLCC - Leaded 0.1uF 50volts 10% X7R 2.5mm LS | 0,206 € |  |  | 1 | 0,206 € | 0.206 |  | 1/1 | 22.016 | 105 | 15 |  | No | Yes | No | BULK | 5.000 | https://www.vishay.com/doc?45171 |  | Product has high popularity and is readily available.
FG18X7R1H104KNT00 | FG18X7R1H104KNT00 | 810-FG18X7R1H104KNT0 | TDK | Multilayer Ceramic Capacitors MLCC - Leaded Multilayer Ceramic Capacitors MLCC - Leaded RAD 50V 0.1uF X7R 10% LS:2.5mm | 0,198 € |  |  | 2 | 0,198 € | 0.396 |  | 1/1 |  | 168 | 24 |  | No | Yes | Yes | BULK | 500 | https://product.tdk.com/system/files/dam/doc/product/capacitor/ceramic/lead-mlcc/catalog/leadmlcc_halogenfree_fg_en.pdf |  | Product has high popularity and is readily available.
0031.8201.G | 0031.8201.G | 693-0031.8201.G | Schurter | Fuse Holder Fuse Holder OGN Fuseholder 5x20 | 0,912 € |  |  | 1 | 0,912 € | 0.912 |  | 1/1 | 54.340 | 97 | 14 |  | No | Yes | No |  | 1.000 | https://us.schurter.com/en/datasheet/typ_OGN.pdf |  | Product has high popularity and is readily available.
22-23-2021 | 22-23-2021 | 538-22-23-2021 | Molex | Headers & Wire Housings Headers & Wire Housings VERT PCB HDR 2P TIN FRICTION LOCK | 0,146 € |  |  | 1 | 0,146 € | 0.146 |  | 1/1 | 156.811 | 112 | 16 |  | No | Yes | Yes | BULK | 17.100 | https://www.molex.com/en-us/products/part-detail-pdf/22232021?display=pdf |  | Product has high popularity and is readily available.
1715750 | 1715750 | 651-1715750 | Phoenix Contact | Fixed Terminal Blocks Fixed Terminal Blocks MKDS 1.5/ 5-5.08 | 2,39 € |  |  | 1 | 2,39 € | 2.39 |  | 1/1 | 230 | 134 | 20 |  | No | Yes | No |  | 250 | https://www.mouser.com/datasheet/3/507/10/phoenix_contact_1715750_en.pdf |  | Product has high popularity and is readily available.
1715721 | 1715721 | 651-1715721 | Phoenix Contact | Fixed Terminal Blocks Fixed Terminal Blocks 2P 5.08mm 90DEG | 1,12 € |  |  | 1 | 1,12 € | 1.12 |  | 1/1 | 5.368 | 105 | 15 |  | No | Yes | No |  | 250 | https://www.mouser.com/datasheet/3/507/7/phoenix_contact_1715721_en.pdf |  | Product has high popularity and is readily available.
5747844-4 | 5747844-4 | 571-5747844-4 | TE Connectivity | D-Sub Standard Connectors D-Sub Standard Connectors RECP FRNT MTL SHL 9P | 2,26 € |  |  | 1 | 2,26 € | 2.26 |  | 1/1 | 7.624 | 70 | 10 |  | No | Yes | No | TRAY | 130 | https://www.te.com/commerce/DocumentDelivery/DDEController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 Section&DocLang=English&PartCntxt=5747844-4&DocFormat=pdf |  | Product has high popularity and is readily available.
NFD17E09PA4E1DA | NFD17E09PA4E1DA | 523-NFD17E09PA4E1DA | Amphenol | D-Sub Standard Connectors D-Sub Standard Connectors D SUB STAMPED PIN MINIATURE MA | 2,91 € |  |  | 1 | 2,91 € | 2.91 |  | 1/1 | 1.381 | 70 | 10 |  | No | Yes | No | TRAY | 2.106 | https://cdn.amphenol-cs.com/media/wysiwyg/files/drawing/p-nfd17-xxxpa-4e1d-a.pdf |  | Product has moderate popularity and is readily available.
1988587 | 1988587 | 651-1988587 | Phoenix Contact | Fixed Terminal Blocks Fixed Terminal Blocks MKDS 1.5/ 2-5.08-RD | 0,92 € |  |  | 3 | 0,92 € | 2.76 |  | 1/1 | 61 | 43 | 7 |  | No | Yes | No |  | 50 | https://www.mouser.com/datasheet/3/507/7/phoenix_contact_1988587_en.pdf |  | Product has moderate popularity and is readily available.
 |  | TOTAL DE COSTOS |  |  |  |  |  |  |  | 63.863

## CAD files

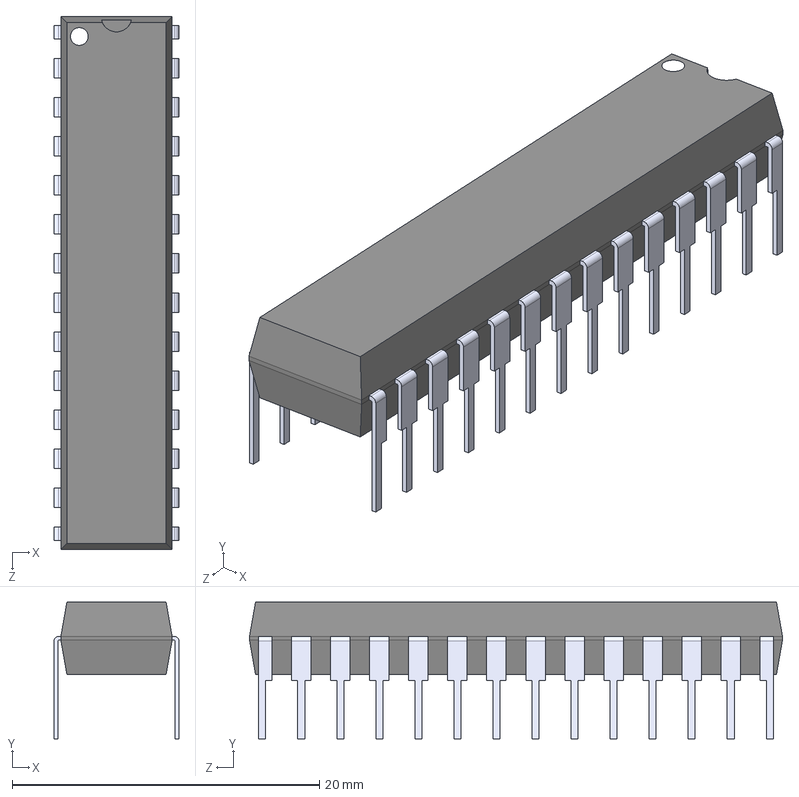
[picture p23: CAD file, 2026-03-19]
KiCad/Fitxers/PIC24HJ128GP502-I_SP/PIC24HJ128GP502-I_SP.step
8.13 x 8.89 x 34.7 mm

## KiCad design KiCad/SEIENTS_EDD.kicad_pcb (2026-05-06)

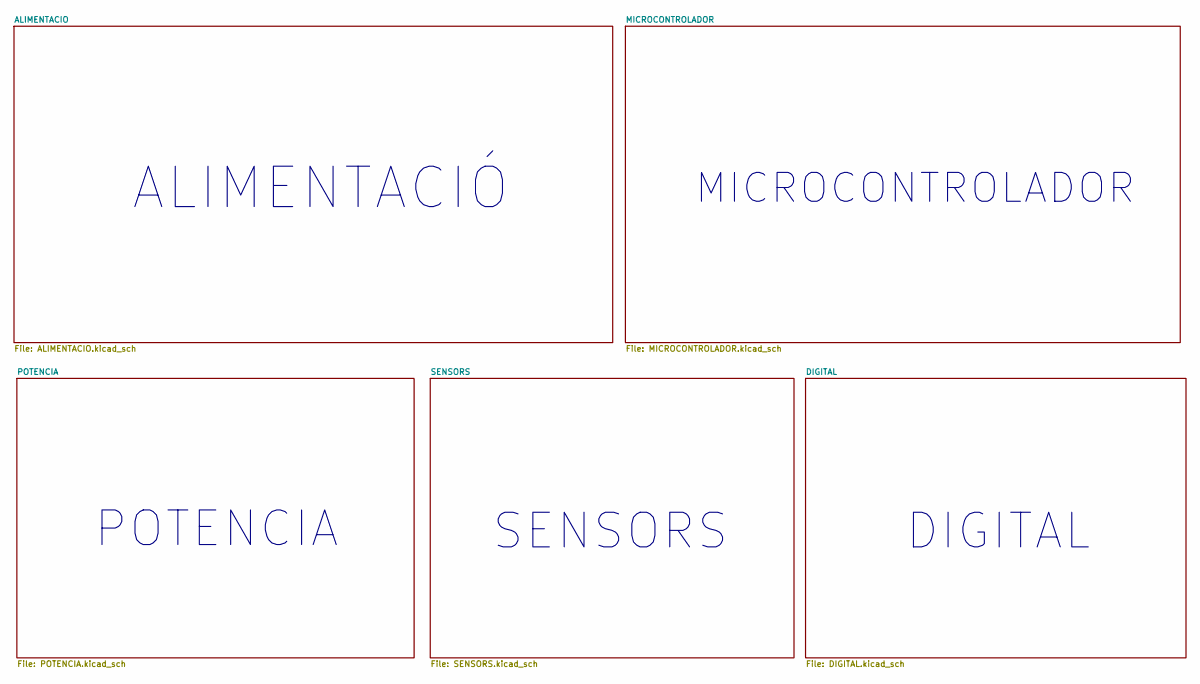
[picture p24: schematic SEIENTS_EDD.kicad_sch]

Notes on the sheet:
SENSORS
DIGITAL
POTENCIA
ALIMENTACIÓ
MICROCONTROLADOR

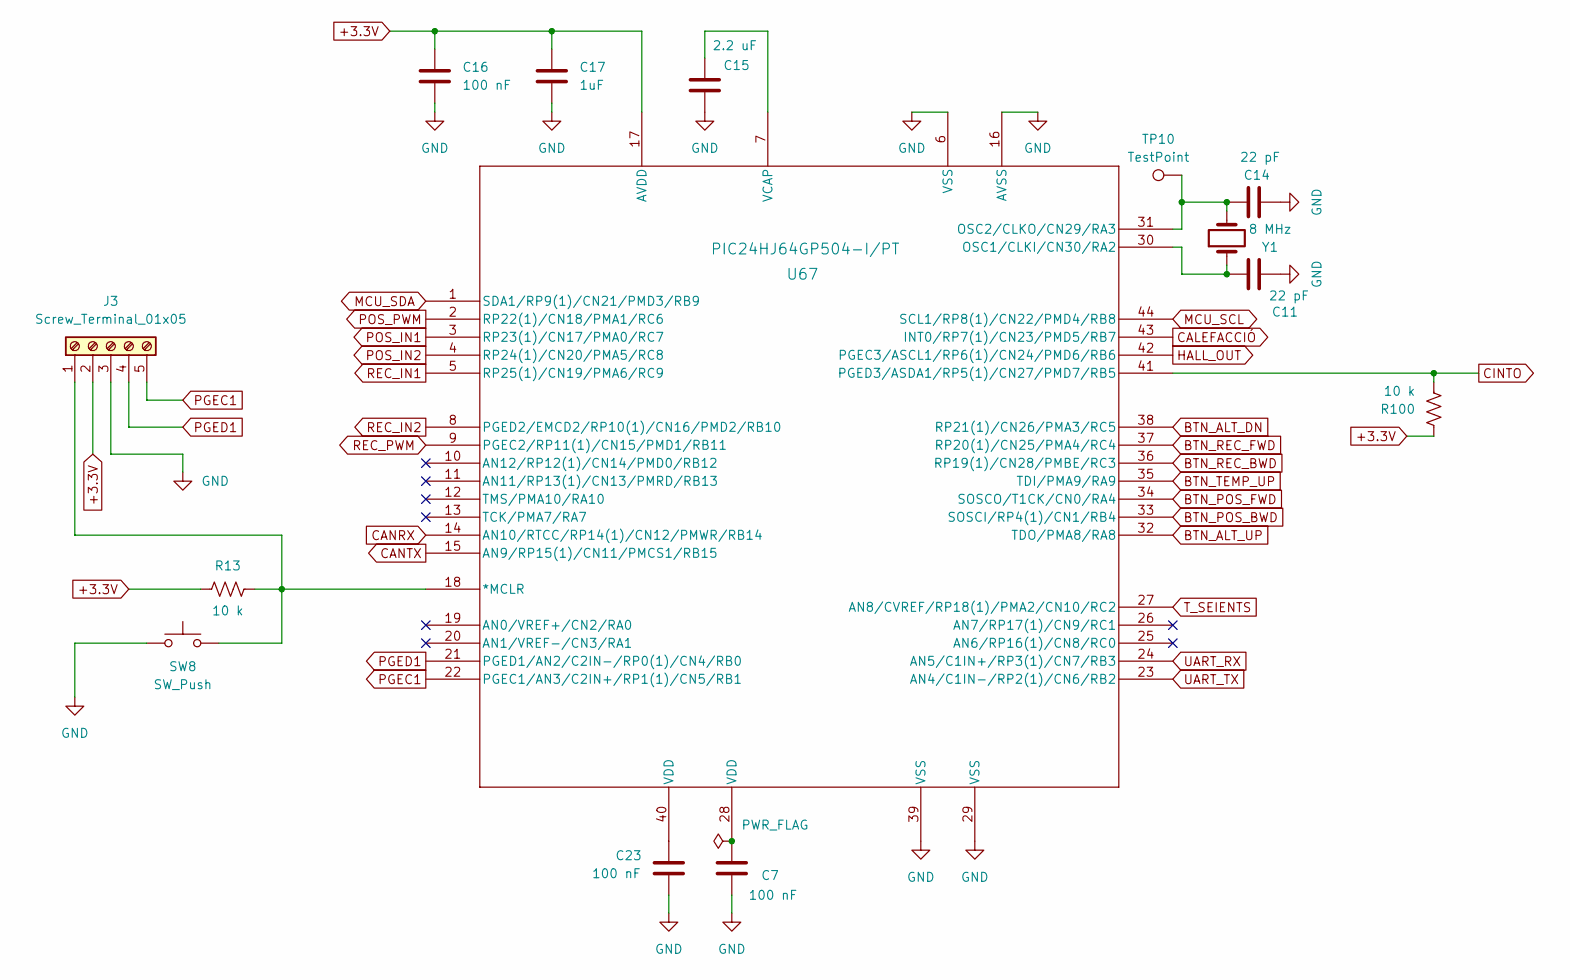
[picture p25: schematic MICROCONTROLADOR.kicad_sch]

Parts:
C7, C16, C23: 100 nF; C_0805_2012Metric
C11, C14: 22 pF; C_0805_2012Metric
C15: 2.2 uF; C_0805_2012Metric
C17: 1uF; C_0805_2012Metric
J3: Screw_Terminal_01x05; TerminalBlock_Phoenix_MKDS-1,5-5-5.08_1x05_P5.08mm_Horizont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
R13, R100: 10 k; R_0805_2012Metric
SW8: SW_Push; SW_Push_SPST_NO_Alps_SKRK
TP10: TestPoint; TestPoint_Pad_D1.0mm
U67: PIC24HJ64GP504-I/PT; TQFP44_10x10MC_MCH-L
Y1: 8 MHz; Crystal_HC49-4H_Vertical

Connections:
+3.3V: C16.1, C17.1, J3.2, R13.1, R100.2, U67.17 (AVDD); also elsewhere on the board
BTN_ALT_DN: U67.38 (RP21(1)/CN26/PMA3/RC5); also elsewhere on the board
BTN_ALT_UP: U67.32 (TDO/PMA8/RA8); also elsewhere on the board
BTN_POS_BWD: U67.33 (SOSCI/RP4(1)/CN1/RB4); also elsewhere on the board
BTN_POS_FWD: U67.34 (SOSCO/T1CK/CN0/RA4); also elsewhere on the board
BTN_REC_BWD: U67.36 (RP19(1)/CN28/PMBE/RC3); also elsewhere on the board
BTN_REC_FWD: U67.37 (RP20(1)/CN25/PMA4/RC4); also elsewhere on the board
BTN_TEMP_UP: U67.35 (TDI/PMA9/RA9); also elsewhere on the board
CALEFACCIÓ: U67.43 (INT0/RP7(1)/CN23/PMD5/RB7); also elsewhere on the board
CANRX: U67.14 (AN10/RTCC/RP14(1)/CN12/PMWR/RB14); also elsewhere on the board
CANTX: U67.15 (AN9/RP15(1)/CN11/PMCS1/RB15); also elsewhere on the board
CINTO: R100.1, U67.41 (PGED3/ASDA1/RP5(1)/CN27/PMD7/RB5); also elsewhere on the board
GND: C7.2, C11.2, C14.2, C15.1, C16.2, C17.2, C23.2, J3.3, SW8.1, U67.6 (VSS), U67.16 (AVSS), U67.29 (VSS), U67.39 (VSS); also elsewhere on the board
HALL_OUT: U67.42 (PGEC3/ASCL1/RP6(1)/CN24/PMD6/RB6); also elsewhere on the board
MCU_SCL: U67.44 (SCL1/RP8(1)/CN22/PMD4/RB8); also elsewhere on the board
MCU_SDA: U67.1 (SDA1/RP9(1)/CN21/PMD3/RB9); also elsewhere on the board
unnamed: C7.1, U67.28 (VDD)
unnamed: C23.1, U67.40 (VDD)
unnamed: J3.1, R13.2, SW8.2, U67.18 (*MCLR)
unnamed: C11.1, U67.30 (OSC1/CLKI/CN30/RA2), Y1.1
unnamed: C14.1, TP10.1, U67.31 (OSC2/CLKO/CN29/RA3), Y1.2
unnamed: C15.2, U67.7 (VCAP)
PGEC1: J3.5, U67.22 (PGEC1/AN3/C2IN+/RP1(1)/CN5/RB1)
PGED1: J3.4, U67.21 (PGED1/AN2/C2IN-/RP0(1)/CN4/RB0)
POS_IN1: U67.3 (RP23(1)/CN17/PMA0/RC7); also elsewhere on the board
POS_IN2: U67.4 (RP24(1)/CN20/PMA5/RC8); also elsewhere on the board
POS_PWM: U67.2 (RP22(1)/CN18/PMA1/RC6); also elsewhere on the board
REC_IN1: U67.5 (RP25(1)/CN19/PMA6/RC9); also elsewhere on the board
REC_IN2: U67.8 (PGED2/EMCD2/RP10(1)/CN16/PMD2/RB10); also elsewhere on the board
REC_PWM: U67.9 (PGEC2/RP11(1)/CN15/PMD1/RB11); also elsewhere on the board
T_SEIENTS: U67.27 (AN8/CVREF/RP18(1)/PMA2/CN10/RC2); also elsewhere on the board
UART_RX: U67.24 (AN5/C1IN+/RP3(1)/CN7/RB3); also elsewhere on the board
UART_TX: U67.23 (AN4/C1IN-/RP2(1)/CN6/RB2); also elsewhere on the board

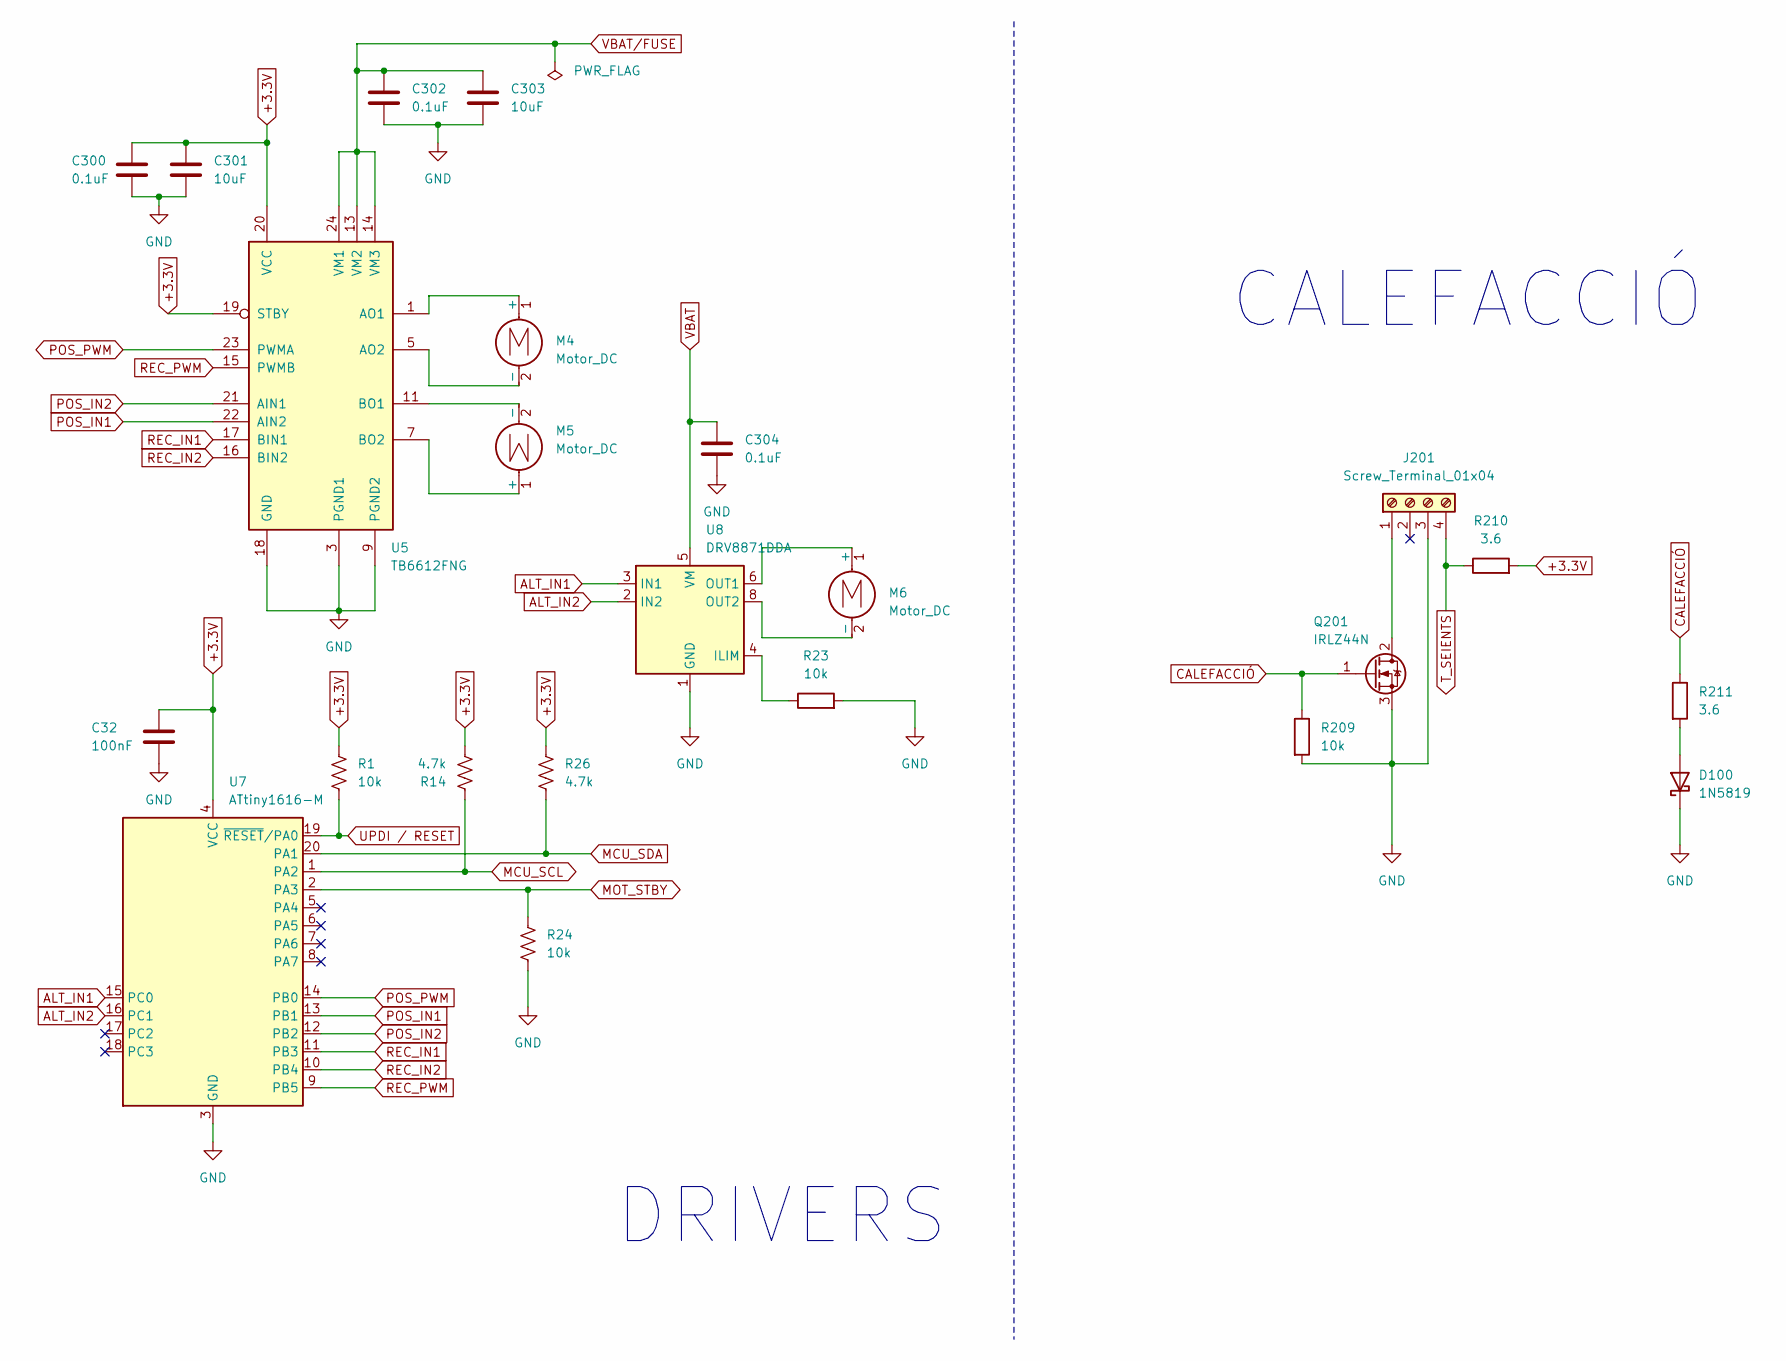
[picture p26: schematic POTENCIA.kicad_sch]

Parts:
C32: 100nF; C_0805_2012Metric
C300, C302, C304: 0.1uF; C_0805_2012Metric
C301, C303: 10uF; CP_Radial_D5.0mm_P2.50mm
D100: 1N5819; D_DO-41_SOD81_P10.16mm_Horizontal
J201: Screw_Terminal_01x04; TerminalBlock_Phoenix_MKDS-1,5-4-5.08_1x04_P5.08mm_Horizont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
M4, M5, M6: Motor_DC; TerminalBlock_Phoenix_MKDS-1,5-2-5.08_1x02_P5.08mm_Horizont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
Q201: IRLZ44N; TO-220-3_Vertical
R1, R23, R24, R209: 10k; R_0805_2012Metric
R14, R26: 4.7k; R_0805_2012Metric
R210, R211: 3.6; R_0805_2012Metric
U5: TB6612FNG; SSOP-24_5.3x8.2mm_P0.65mm
U7: ATtiny1616-M; VQFN-20-1EP_3x3mm_P0.4mm_EP1.7x1.7mm
U8: DRV8871DDA; Texas_HTSOP-8-1EP_3.9x4.9mm_P1.27mm_EP2.95x4.9mm_Mask2.4x3.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

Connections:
+3.3V: C32.1, C300.1, C301.1, R1.1, R14.2, R26.1, R210.2, U5.19 (STBY), U5.20 (VCC), U7.4 (VCC); also elsewhere on the board
ALT_IN1: U7.15 (PC0), U8.3 (IN1)
ALT_IN2: U7.16 (PC1), U8.2 (IN2)
CALEFACCIÓ: Q201.1 (G), R209.1, R211.1; also elsewhere on the board
GND: C32.2, C300.2, C301.2, C302.2, C303.2, C304.2, D100.1 (K), J201.3, Q201.3 (S), R23.2, R24.2, R209.2, U5.3 (PGND1), U5.4 (PGND1), U5.9 (PGND2), U5.10 (PGND2), U5.18 (GND), U7.3 (GND), U7.21 (GND), U8.1 (GND), U8.7 (GND), U8.9 (GND); also elsewhere on the board
MCU_SCL: R14.1, U7.1 (PA2); also elsewhere on the board
MCU_SDA: R26.2, U7.20 (PA1); also elsewhere on the board
MOT_STBY: R24.1, U7.2 (PA3)
unnamed: D100.2 (A), R211.2
unnamed: J201.1, Q201.2 (D)
unnamed: M4.1 (+), U5.1 (AO1), U5.2 (AO1)
unnamed: M4.2 (-), U5.5 (AO2), U5.6 (AO2)
unnamed: M5.1 (+), U5.7 (BO2), U5.8 (BO2)
unnamed: M5.2 (-), U5.11 (BO1), U5.12 (BO1)
unnamed: M6.1 (+), U8.6 (OUT1)
unnamed: M6.2 (-), U8.8 (OUT2)
unnamed: R23.1, U8.4 (ILIM)
POS_IN1: U5.22 (AIN2), U7.13 (PB1); also elsewhere on the board
POS_IN2: U5.21 (AIN1), U7.12 (PB2); also elsewhere on the board
POS_PWM: U5.23 (PWMA), U7.14 (PB0); also elsewhere on the board
REC_IN1: U5.17 (BIN1), U7.11 (PB3); also elsewhere on the board
REC_IN2: U5.16 (BIN2), U7.10 (PB4); also elsewhere on the board
REC_PWM: U5.15 (PWMB), U7.9 (PB5); also elsewhere on the board
T_SEIENTS: J201.4, R210.1; also elsewhere on the board
UPDI / RESET: R1.2, U7.19 (~RESET/PA0)
VBAT: C304.1, U8.5 (VM); also elsewhere on the board
VBAT/FUSE: C302.1, C303.1, U5.13 (VM2), U5.14 (VM3), U5.24 (VM1); also elsewhere on the board

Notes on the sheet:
CALEFACCIÓ
DRIVERS

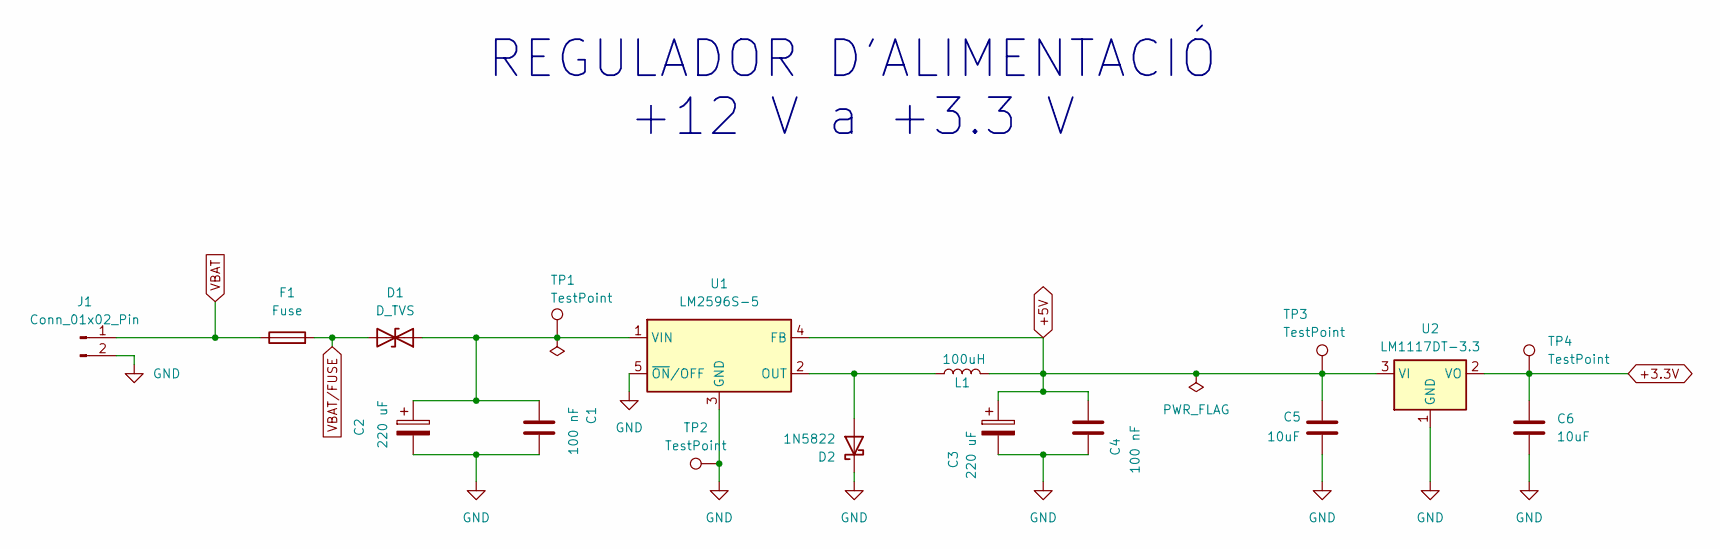
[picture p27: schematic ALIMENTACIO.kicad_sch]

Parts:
C1, C4: 100 nF; C_0805_2012Metric
C2, C3: 220 uF; C_0805_2012Metric
C5, C6: 10uF; C_0805_2012Metric
D1: D_TVS; D_SMA
D2: 1N5822; D_DO-201AD_P15.24mm_Horizontal
F1: Fuse; Fuseholder_Cylinder-5x20mm_Schurter_0031_8201_Horizontal_Op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
J1: Conn_01x02_Pin; TerminalBlock_Phoenix_MKDS-1,5-2-5.08_1x02_P5.08mm_Horizont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
L1: 100uH; L_Radial_D10.0mm_P5.00mm_Fastron_07M
TP1, TP2, TP3, TP4: TestPoint; TestPoint_Pad_D1.0mm
U1: LM2596S-5; TO-263-5_TabPin3
U2: LM1117DT-3.3; TO-252-3_TabPin2

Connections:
+3.3V: C6.1, TP4.1, U2.2 (VO); also elsewhere on the board
+5V: C3.1, C4.1, C5.1, L1.2, TP3.1, U1.4 (FB), U2.3 (VI); also elsewhere on the board
GND: C1.1, C2.2, C3.2, C4.2, C5.2, C6.2, D2.1 (K), J1.2, TP2.1, U1.3 (GND), U1.5 (~ON/OFF), U2.1 (GND); also elsewhere on the board
unnamed: C1.2, C2.1, D1.1 (A1), TP1.1, U1.1 (VIN)
unnamed: D2.2 (A), L1.1, U1.2 (OUT)
VBAT: F1.1, J1.1; also elsewhere on the board
VBAT/FUSE: D1.2 (A2), F1.2; also elsewhere on the board

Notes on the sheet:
REGULADOR D'ALIMENTACIÓ +12 V a +3.3 V

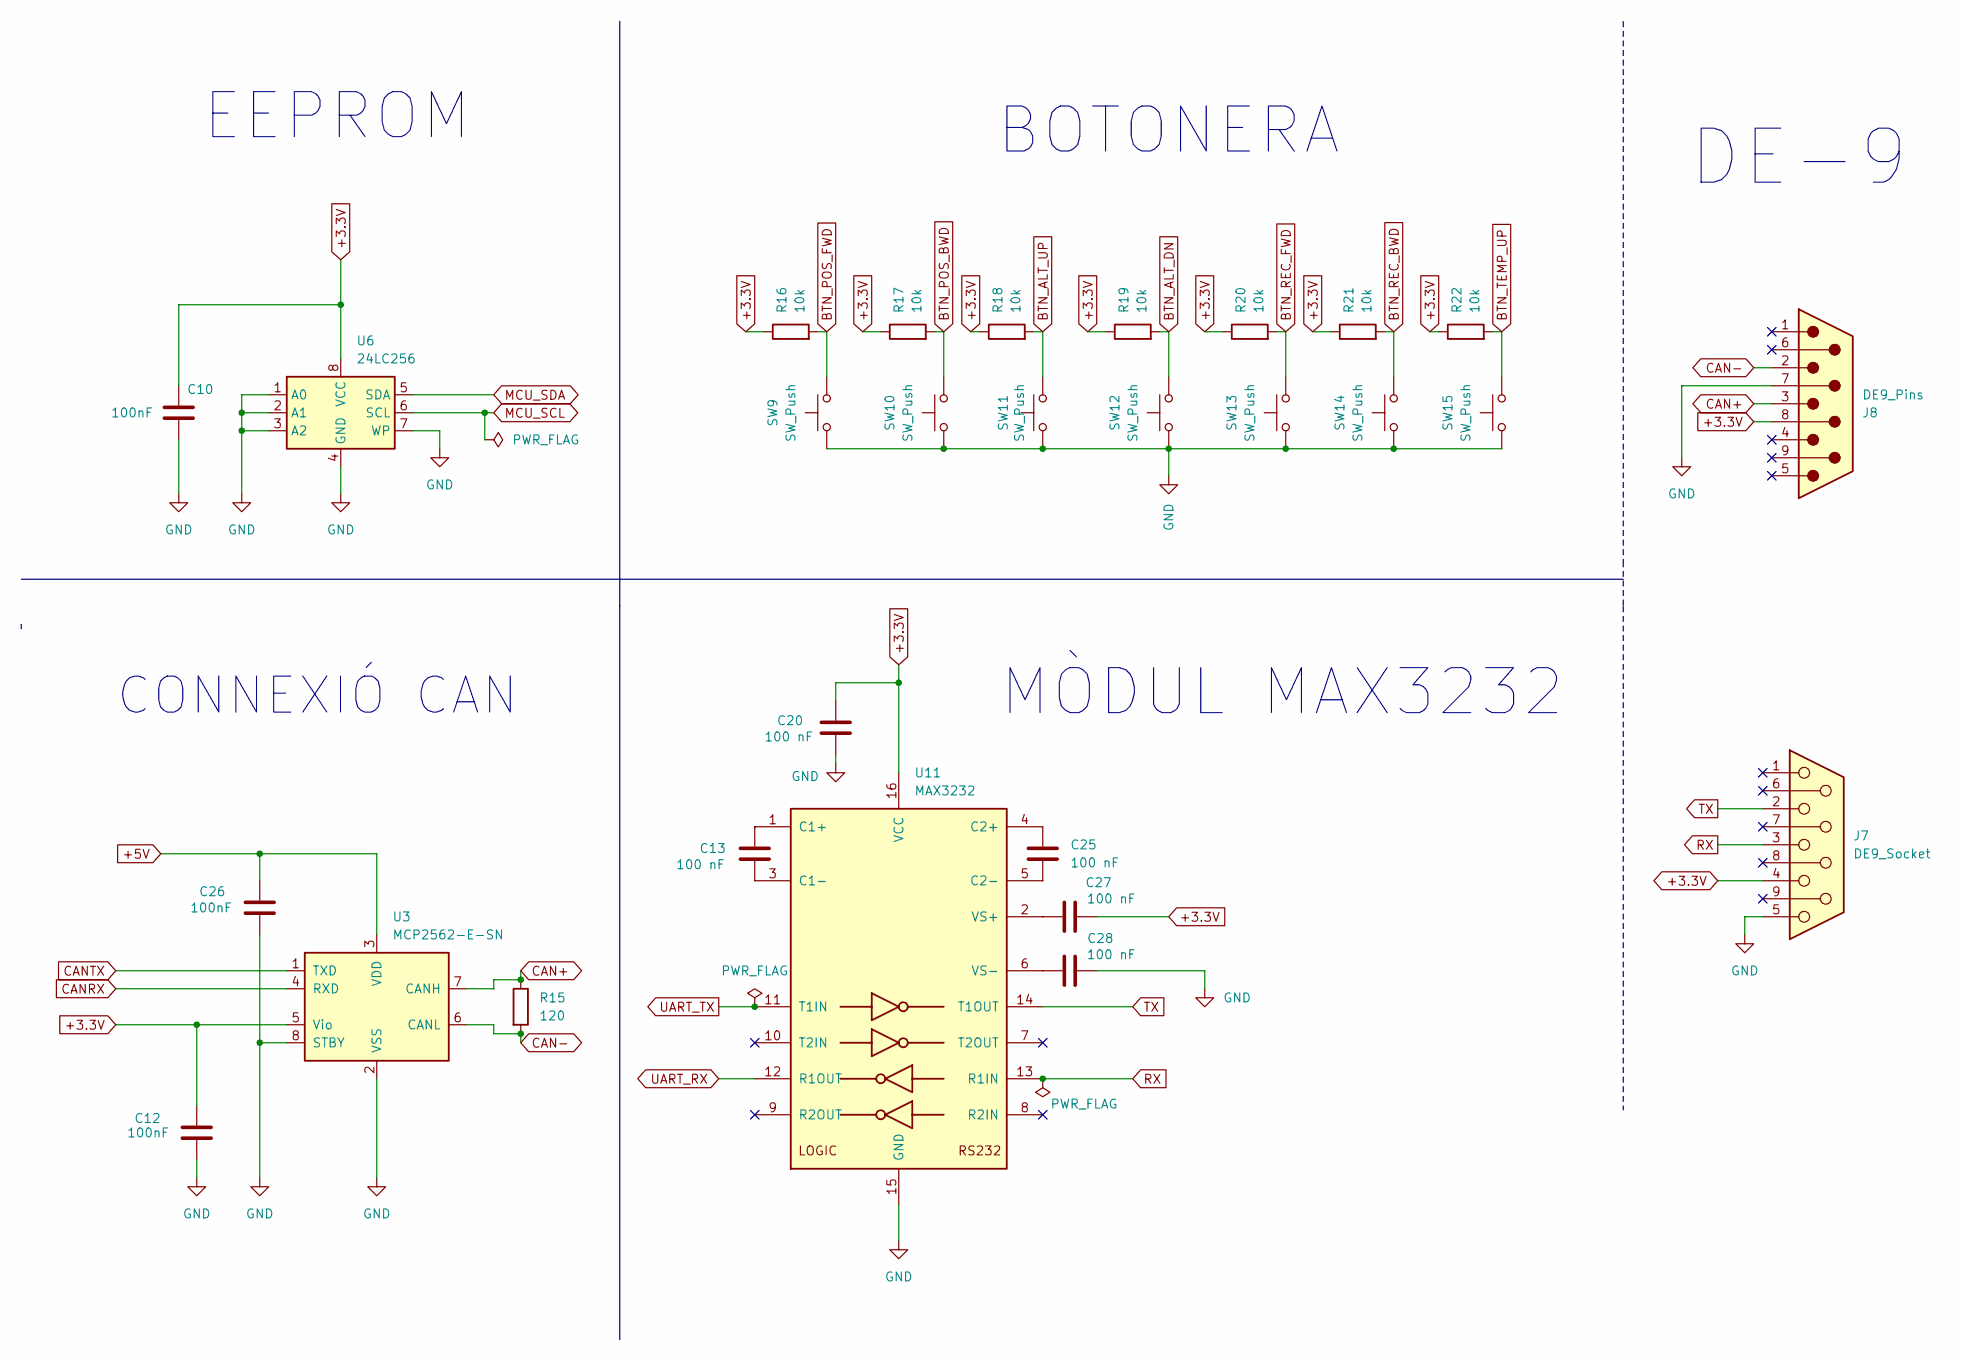
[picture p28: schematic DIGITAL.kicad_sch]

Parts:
C10, C12, C26: 100nF; C_0805_2012Metric
C13, C20, C25, C27, C28: 100 nF; C_0805_2012Metric
J7: DE9_Socket; DSUB-9_Socket_Horizontal_P2.77x2.84mm_EdgePinOffset4.94mm_H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
J8: DE9_Pins; DSUB-9_Pins_Horizontal_P2.77x2.84mm_EdgePinOffset4.94mm_Hou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
R15: 120; R_0805_2012Metric
R16, R17, R18, R19, R20, R21, R22: 10k; R_0805_2012Metric
SW9, SW10, SW11, SW12, SW13, SW14, SW15: SW_Push; SW_Push_SPST_NO_Alps_SKRK
U3: MCP2562-E-SN; SOIC-8_3.9x4.9mm_P1.27mm
U6: 24LC256; SOIC-8_3.9x4.9mm_P1.27mm
U11: MAX3232; SOIC-16_3.9x9.9mm_P1.27mm

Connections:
+3.3V: C10.2, C12.2, C20.1, C27.2, J7.4, J8.8, R16.1, R17.1, R18.1, R19.1, R20.1, R21.1, R22.1, U3.5 (Vio), U6.8 (VCC), U11.16 (VCC); also elsewhere on the board
+5V: C26.2, U3.3 (VDD); also elsewhere on the board
BTN_ALT_DN: R19.2, SW12.2; also elsewhere on the board
BTN_ALT_UP: R18.2, SW11.2; also elsewhere on the board
BTN_POS_BWD: R17.2, SW10.2; also elsewhere on the board
BTN_POS_FWD: R16.2, SW9.2; also elsewhere on the board
BTN_REC_BWD: R21.2, SW14.2; also elsewhere on the board
BTN_REC_FWD: R20.2, SW13.2; also elsewhere on the board
BTN_TEMP_UP: R22.2, SW15.2; also elsewhere on the board
CAN+: J8.3, R15.1, U3.7 (CANH)
CAN-: J8.2, R15.2, U3.6 (CANL)
CANRX: U3.4 (RXD); also elsewhere on the board
CANTX: U3.1 (TXD); also elsewhere on the board
GND: C10.1, C12.1, C20.2, C26.1, C28.2, J7.5, J8.7, SW9.1, SW10.1, SW11.1, SW12.1, SW13.1, SW14.1, SW15.1, U3.2 (VSS), U3.8 (STBY), U6.1 (A0), U6.2 (A1), U6.3 (A2), U6.4 (GND), U6.7 (WP), U11.15 (GND); also elsewhere on the board
MCU_SCL: U6.6 (SCL); also elsewhere on the board
MCU_SDA: U6.5 (SDA); also elsewhere on the board
unnamed: C13.1, U11.1 (C1+)
unnamed: C13.2, U11.3 (C1-)
unnamed: C25.1, U11.4 (C2+)
unnamed: C25.2, U11.5 (C2-)
unnamed: C27.1, U11.2 (VS+)
unnamed: C28.1, U11.6 (VS-)
RX: J7.3, U11.13 (R1IN)
TX: J7.2, U11.14 (T1OUT)
UART_RX: U11.12 (R1OUT); also elsewhere on the board
UART_TX: U11.11 (T1IN); also elsewhere on the board

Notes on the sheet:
BOTONERA
EEPROM
MÒDUL MAX3232
DE-9
CONNEXIÓ CAN

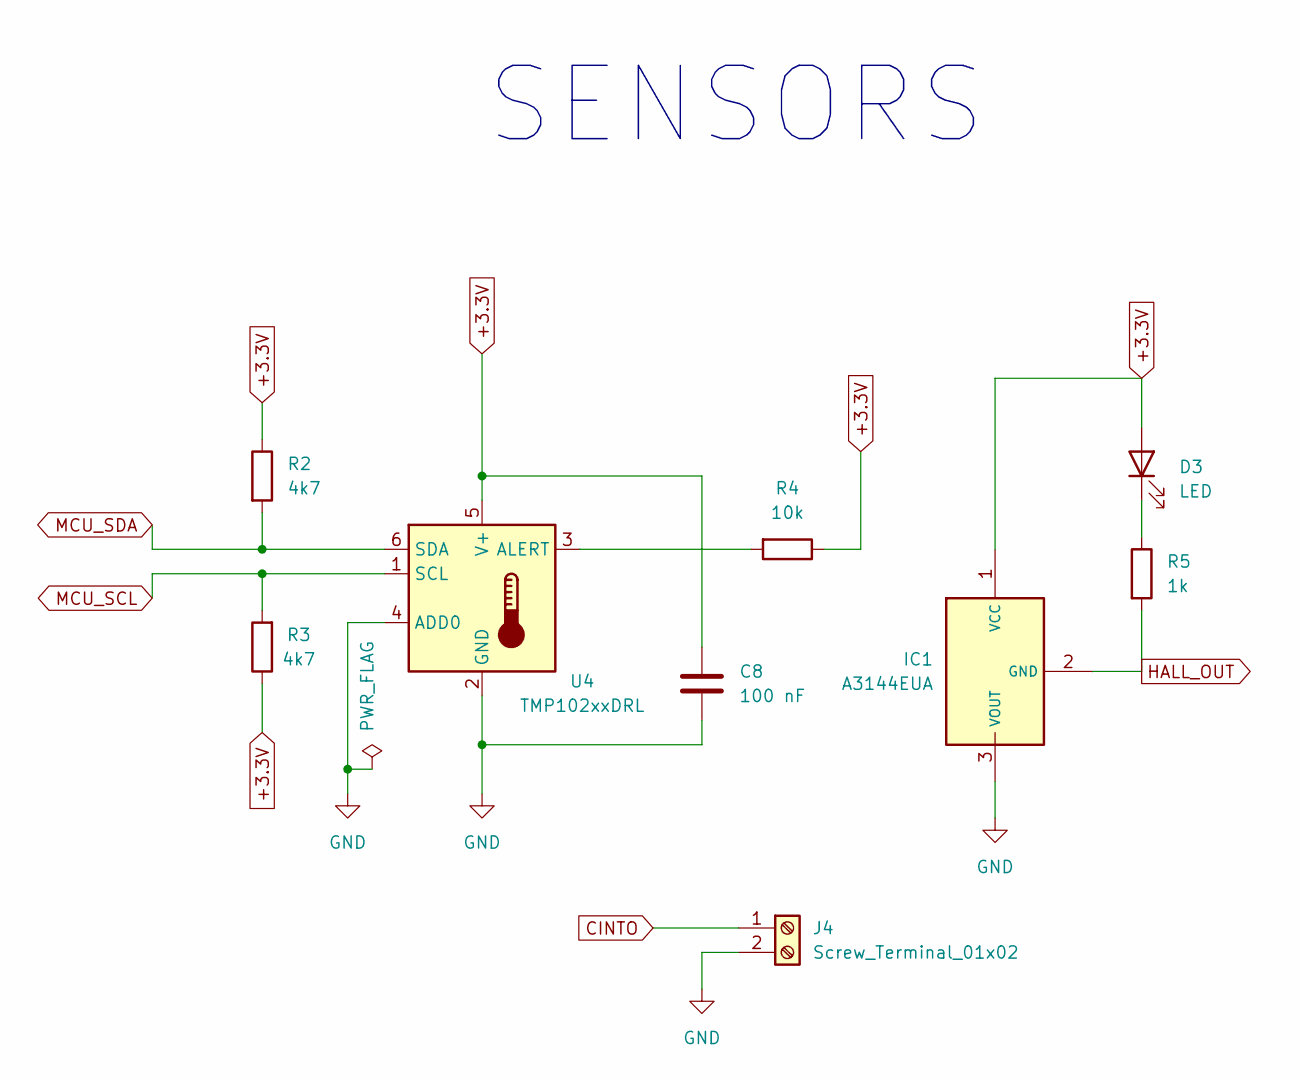
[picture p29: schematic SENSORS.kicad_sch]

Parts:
C8: 100 nF; C_0805_2012Metric
D3: LED; LED_D3.0mm
IC1: A3144EUA; Manufacturer_Part_Number A3144EUA
J4: Screw_Terminal_01x02; TerminalBlock_Phoenix_MKDS-1,5-2-5.08_1x02_P5.08mm_Horizont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
R2, R3: 4k7; R_0805_2012Metric
R4: 10k; R_0805_2012Metric
R5: 1k; R_0805_2012Metric
U4: TMP102xxDRL; SOT-563

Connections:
+3.3V: C8.1, D3.2 (A), IC1.1 (VCC), R2.1, R3.1, R4.1, U4.5 (V+); also elsewhere on the board
CINTO: J4.1; also elsewhere on the board
GND: C8.2, IC1.3 (VOUT), J4.2, U4.2 (GND), U4.4 (ADD0); also elsewhere on the board
HALL_OUT: IC1.2 (GND), R5.2; also elsewhere on the board
MCU_SCL: R3.2, U4.1 (SCL); also elsewhere on the board
MCU_SDA: R2.2, U4.6 (SDA); also elsewhere on the board
unnamed: D3.1 (K), R5.1
unnamed: R4.2, U4.3 (ALERT)

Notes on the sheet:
SENSORS

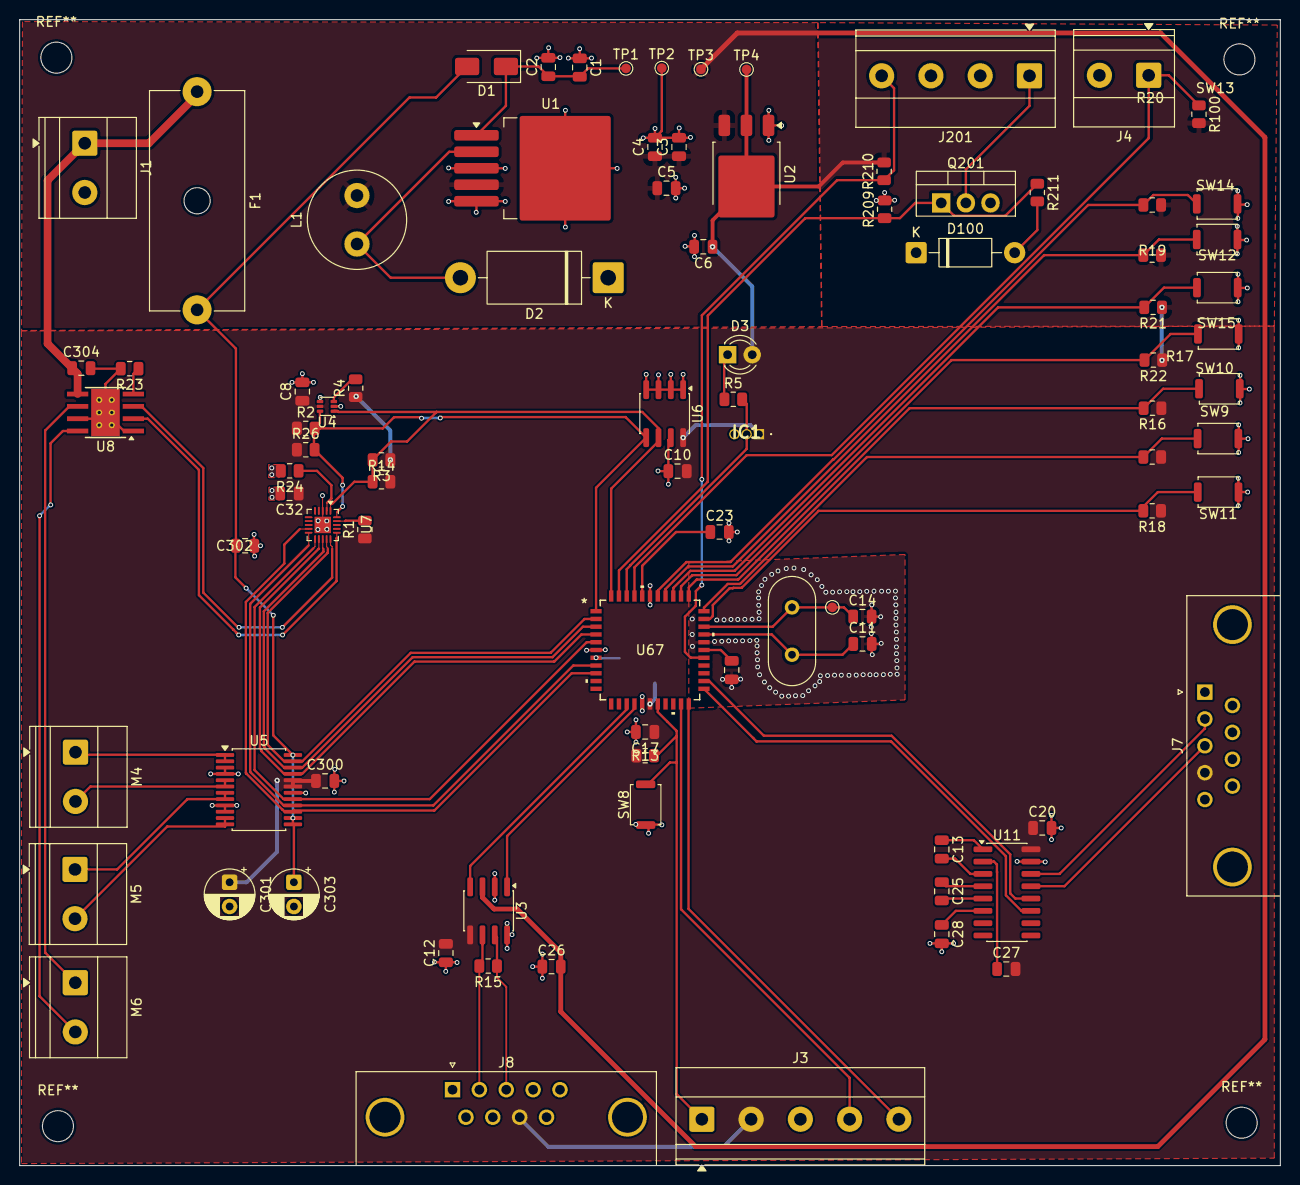
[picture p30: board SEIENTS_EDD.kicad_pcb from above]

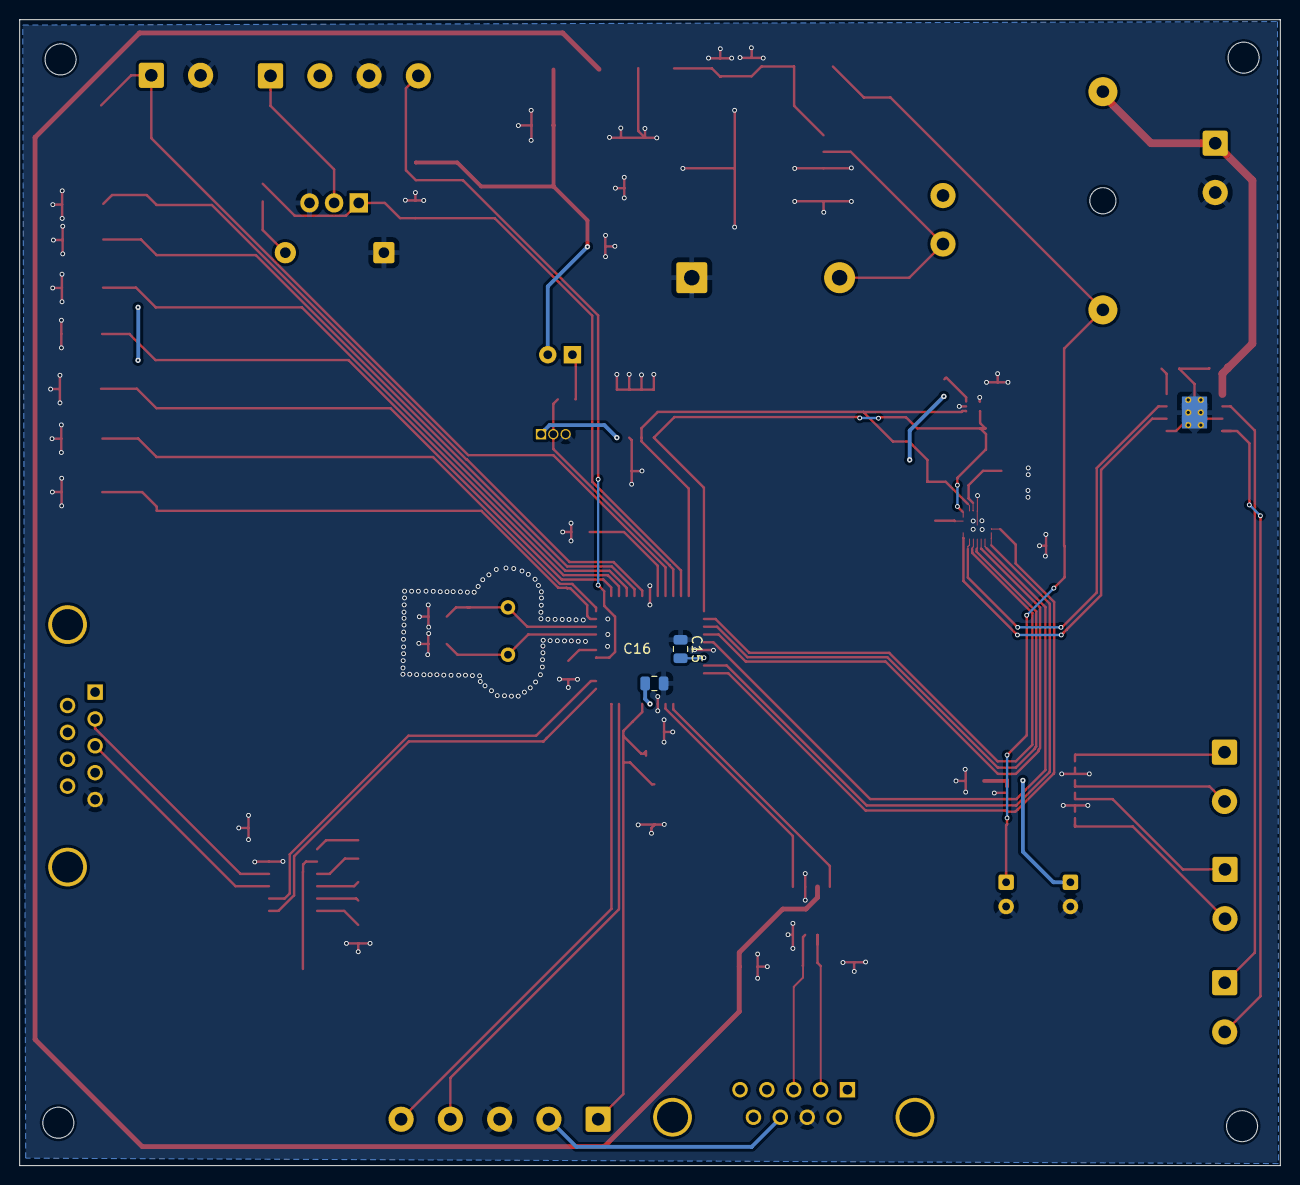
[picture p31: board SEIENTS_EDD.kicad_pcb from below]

Board: 2 copper layers, 130.0 x 118.2 mm, 91 parts (2 on the bottom side), 63 nets.

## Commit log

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2026-03-12 PROJECTE CREAT
    [SEIENTS_EDD.kicad_pcb, SEIENTS_EDD.kicad_sch]
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2026-03-19 Primer Esquematic
    [ALIMENTACIO.kicad_sch, MICROCONTROLADOR.kicad_sch, PIC24HJ128GP502-I_SP.step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]
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2026-03-19 Noms blocs
    [SEIENTS_EDD.kicad_sch]
2026-03-23 Canvis a sensors
    [SENSORS.kicad_sch]
2026-03-24 cambios en la parte de motors (aun incompleto debido a la falta de conexion con el microcontrolador
    [DRIVERS(MOTORS).kicad_sch]
2026-03-24 Canvis a la part d'alimentació
    [ALIMENTACIO.kicad_sch]
2026-03-24 Canvis a l'alimentació: afegits TVS i Fusible
    [ALIMENTACIO.kicad_sch]
2026-03-24 Canvis a l'alimentació: afegides capacitats de desacoblament
    [ALIMENTACIO.kicad_sch]
2026-03-24 Canvis a l'alimentació: Problemes ERC solventats
    [ALIMENTACIO.kicad_sch]
2026-03-24 Canvis a l'alimentació: part acabada
    [ALIMENTACIO.kicad_sch]
2026-03-24 Canvis als SENSORS: fet al 70%
    [SENSORS.kicad_sch]
2026-03-25 Canvis als SENSORS: fet al 90%
    [SENSORS.kicad_sch]
2026-03-25 Canvis als SENSORS: Sensors acabats
    [SENSORS.kicad_sch]
2026-03-25 Afegit CAN
    [CAN.kicad_sch, DRIVERS(MOTORS).kicad_sch, MICROCONTROLADOR.kicad_sch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]
2026-03-25 Modificació
    [ALIMENTACIO.kicad_sch, CAN.kicad_sch, DRIVERS(MOTORS).kicad_sch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]
2026-03-25 Cambios en motors (etiqetas)
    [DRIVERS(MOTORS).kicad_sch, MICROCONTROLADOR.kicad_sch]
2026-03-26 Canvis al KICAD
    [DRIVERS(MOTORS).kicad_sch, SENSORS.kicad_sch]
2026-03-26 Afegist el MOSFET
    [DRIVERS(MOTORS).kicad_sch, MICROCONTROLADOR.kicad_sch, MOSFET.kicad_sch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]
2026-03-26 Modificacio Labels
    [ALIMENTACIO.kicad_sch, DRIVERS(MOTORS).kicad_sch, MICROCONTROLADOR.kicad_sch]
2026-03-26 PINS MICRO
    [BOTONERA.kicad_sch, MICROCONTROLADOR.kicad_sch]
2026-03-30 Modificació README
    [MICROCONTROLADOR.kicad_sch]
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2026-04-07 cambios mejora ERC
    [ALIMENTACIO.kicad_sch, BOTONERA.kicad_sch, CAN.kicad_sch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]
2026-04-07 Arreglada la EEPROM
    [EEPROM.kicad_sch]
2026-04-07 Arreglat el DE-9
    [DE9.kicad_sch, SEIENTS_EDD.kicad_sch]
2026-04-07 ArregLATS ERRORS ERC
    [CAN.kicad_sch, DE9.kicad_sch, EEPROM.kicad_sch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]
2026-04-07 Arreglats errors i modificació del microcontrolador
    [MICROCONTROLADOR.kicad_sch, MÒDULMAX3232.kicad_sch, SEIENTS_EDD.kicad_sch]
2026-04-07 Arreglat lo del microcontrolador
    [MICROCONTROLADOR.kicad_sch]
2026-04-07 Arreglat lo del MAX
    [MÒDULMAX3232.kicad_sch]
2026-04-07 Modificacions al MICROCONTROLADOR
    [MICROCONTROLADOR.kicad_sch]
2026-04-08 Cambio en la parte de motores y drivers
    [DRIVERS(MOTORS).kicad_sch, MICROCONTROLADOR.kicad_sch, MÒDULMAX3232.kicad_sch]
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2026-04-08 Modificacions al DE-9
    [DE9.kicad_sch]
2026-04-08 canvia al microcontrolador
    [EEPROM.kicad_sch, MICROCONTROLADOR.kicad_sch, SENSORS.kicad_sch]
2026-04-08 Modificacions Micro
    [ALIMENTACIO.kicad_sch, CAN.kicad_sch, DE9.kicad_sch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]
2026-04-08 Començat el LAYOUT
    [ALIMENTACIO.kicad_sch, BOTONERA.kicad_sch, CAN.kicad_sch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]
2026-04-09 canvis a motors i layout
    [DRIVERS(MOTORS).kicad_pcb, DRIVERS(MOTORS).kicad_sch]
2026-04-09 footprints asignados
    [ALIMENTACIO.kicad_sch, CAN.kicad_sch, DRIVERS(MOTORS).kicad_sch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]
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2026-04-09 Placement començat
    [SEIENTS_EDD.kicad_pcb]
2026-04-09 canvios en motores
    [SEIENTS_EDD.kicad_pcb]
2026-04-09 Modificat el placement
    [SEIENTS_EDD.kicad_pcb]
2026-04-09 Afegit PIC 44 pins
    [MICROCONTROLADOR.kicad_sch]
2026-04-09 Micro editat simbol
    [MICROCONTROLADOR.kicad_sch]
2026-04-09 Testpoint añadidos
    [ALIMENTACIO.kicad_sch]
2026-04-11 Modificat ETIQUETES MICROCONTROLADOR
    [ALIMENTACIO.kicad_sch, MICROCONTROLADOR.kicad_sch]
2026-04-11 Modificat ETIQUETES MICROCONTROLADOR i errors varis
    [ALIMENTACIO.kicad_sch, BOTONERA.kicad_sch, MICROCONTROLADOR.kicad_sch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]
2026-04-11 Modificació al placement
    [SEIENTS_EDD.kicad_pcb]
2026-04-13 Organització Esquematic, asignacio huellas Test Points i Microcontrolador acabat
    [ALIMENTACIO.kicad_sch, DIGITAL.kicad_sch, MICROCONTROLADOR.kicad_sch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]
2026-04-13 Llibreria afegida
    [SENSORS.kicad_sch]
2026-04-13 Modificació al HALL A3144
    [SENSORS.kicad_sch]
2026-04-13 Modificació als SENSORS
    [SENSORS.kicad_sch]
2026-04-13 cambios en el mosfet
    [MICROCONTROLADOR.kicad_sch, MOSFET.kicad_sch]
2026-04-13 Modificació als ALIMENTACIÓ
    [ALIMENTACIO.kicad_sch]
2026-04-13 Modificació d'errors varis
    [ALIMENTACIO.kicad_sch, MICROCONTROLADOR.kicad_sch, SENSORS.kicad_sch]
2026-04-13 cambios en organizacion
    [ALIMENTACIO.kicad_sch, BOTONERA.kicad_sch, CAN.kicad_sch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]
2026-04-14 Placement inicial acabat
    [SEIENTS_EDD.kicad_pcb]
2026-04-15 Afegit el BOM
    [SEIENTS_EDD.csv]
2026-04-15 Modificació Placement
    [DIGITAL.kicad_sch, SEIENTS_EDD.kicad_pcb]
2026-04-15 FootPrints Canviats
    [ALIMENTACIO.kicad_sch, POTENCIA.kicad_sch, SEIENTS_EDD.kicad_pcb]
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2026-04-18 Modificació als DRIVERS
    [POTENCIA.kicad_sch]
2026-04-19 cambios en el placement
    [SEIENTS_EDD.kicad_pcb]
2026-04-19 cambios en el placement2
    [SEIENTS_EDD.kicad_pcb]
2026-04-20 Routing V1
    [DIGITAL.kicad_sch, POTENCIA.kicad_sch, SEIENTS_EDD.kicad_pcb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]
2026-04-20 Modificació al routing
    [SEIENTS_EDD.kicad_pcb]
2026-04-21 Routing V2
    [SEIENTS_EDD.kicad_pcb]
2026-04-22 Canvi planos
    [SEIENTS_EDD.kicad_pcb]
2026-04-24 Routing V4
    [SEIENTS_EDD.kicad_pcb]
2026-04-24 avances en kicad
    [SEIENTS_EDD.kicad_pcb]
2026-04-25 cambios en layout
    [SEIENTS_EDD.kicad_pcb]
2026-04-29 Rounting V5
    [SEIENTS_EDD.kicad_pcb]
2026-04-29 Modificació de gerbers i power point
    [SEIENTS_EDD-B_Cu.gbr, SEIENTS_EDD-B_Mask.gbr, SEIENTS_EDD-B_Paste.gbr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]
2026-04-29 Routing V6
    [SEIENTS_EDD.kicad_pcb]
2026-05-03 ROUTING FINAL
    [ALIMENTACIO.kicad_sch, DIGITAL.kicad_sch, MICROCONTROLADOR.kicad_sch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]
2026-05-06 cambios en los costos
    [tabla_costes_pcb_unidades_visibles.xlsx]
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
